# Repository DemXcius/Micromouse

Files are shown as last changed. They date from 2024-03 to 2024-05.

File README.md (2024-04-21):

# Micromouse
# The repository for a third-year engineering design project
This repository contains the design and production files for the Power and Sensor modules of a micro-mouse, as part of the EEE3088F course at UCT 2024 Main Project.

# Project Overview: Micro-Mouse Hardware Design

## What is a Micro-Mouse?
In essence, a micro-mouse is a maze-solving robot. If you're unfamiliar with the concept, watch [Veritasium's](https://www.youtube.com/watch?v=ZMQbHMgK2rw) video to gain a clearer understanding. It's worth noting that while the robots featured in the video may be quite speedy, this micro-mouse will likely (almost certainly) operate at a slower pace. Nonetheless, let the video serve as inspiration.

## Project Description
This project focuses primarily on the design of the micro-mouse's hardware, with some minor software components. The main challenge lies in meeting the project's requirements while adhering to a STRICT budget. To facilitate this endeavor, the project has been divided into four modules: the processor, motherboard, sensing, and power.
The processor and motherboard modules have already been designed and this repository focuses only on the sensing and power modules. 

## Project Modules

### Processor Module: 
This module entails the design of the microcontroller unit responsible for controlling the micro-mouse's actions within the maze. The processor used is an STM32L476.

### Motherboard Module: 
The motherboard serves as the central hub for connecting various hardware components of the micro-mouse. Here, there is leeway as to how the motherboard is designed.

### Sensing Module: 
The project will involve designing and manufacturing the sensing module, which comprises sensors responsible for detecting walls, corners, and other obstacles within the maze.

### Power Module: 
Lastly, the project involves designing and manufacturing the power module, which will provide the necessary electrical power to all components of the micro-mouse.

## Budget Constraint
It's crucial to note that this project had a strict budget constraint imposed. While innovation and creativity are encouraged, all design decisions were made with the budget in mind.

## Project Details:
- Project Focus: Power and sensing module design and manufacturing.
- Connectors: JST PH 2mm pin pitch connector for the battery and a 2x8 (2.54mm pin pitch) pin header for interfacing with the motherboard.
- Budget: $8.25 per board.

## Subsystem Description: Power
- Motor Operation: Controls 2 motors, each capable of drawing up to 200mA, powered by a 1S1P battery.
- Battery Voltage Sensing: Provides an analog connection to sense battery voltage for battery state of charge (SoC) monitoring.
- Battery Charging: Charges the battery from the 5V input pin. Must handle the scenario when 5V is removed.
- ON/OFF Switch: Incorporates an ON/OFF switch with specific power consumption requirements in the OFF and ON states.
  
## Subsystem Description: Sensing
- Sensor Operation: Detects whether there is an obstacle in front of the robot or on its sides.
- Power Saving: Has switching means to save power when not in operation.
- Main Components: 4x TSAL4400 IR LED's, 3x SFH205F photodiodes, 1x LiPo 800mAh 3.7V

- ## Included Files:
- Datasheets: Datasheets for components used in the Power and Sensing modules.
- Production Files: Files required for manufacturing the Power and Sensing module, including Gerber files and Bill of Materials (BOM).
- Schematics: Schematics for Power and Sensing modules.
  
## Usage:
- Clone the repository to access all project files.
- Review the datasheets for component specifications.
- Use the production files for manufacturing the Power or Sensing module PCB's.
- Review and modify the PCB files as needed for customization.
  
- NOTE: Production and files associated with the production were designed and used with [jlcpcb](https://jlcpcb.com/) as the manufacturer in mind.

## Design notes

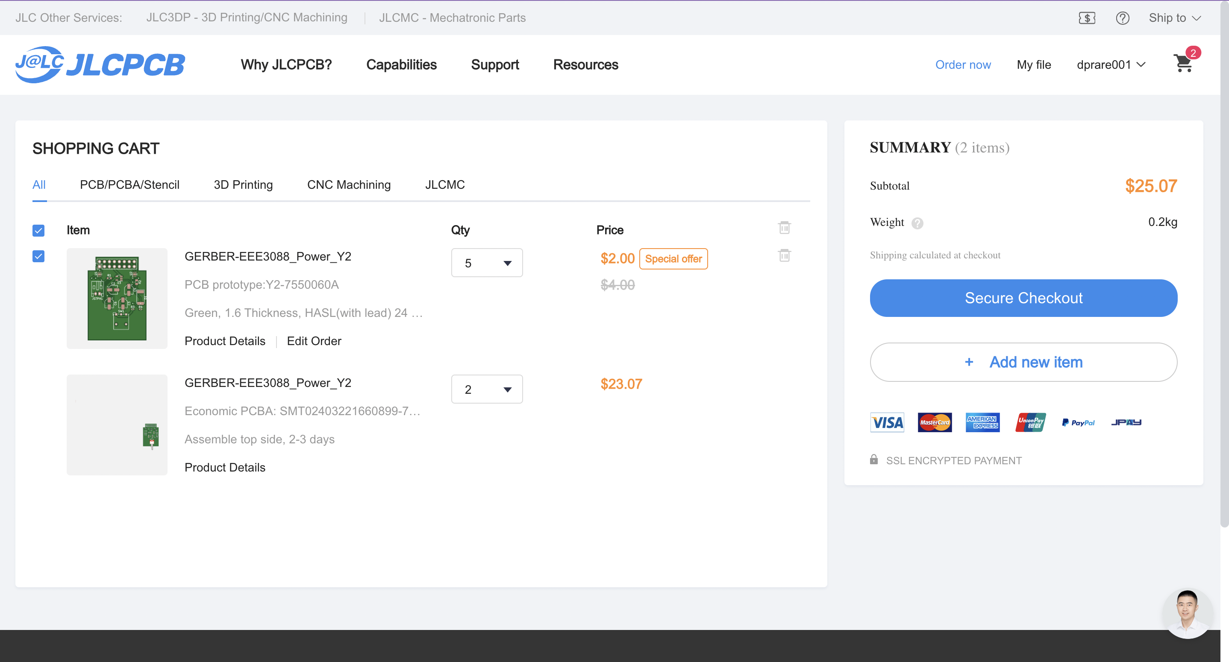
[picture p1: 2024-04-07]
Power Subsystem/EEE3088F_Project_JLCPCBacceptance_DPRARE001.png

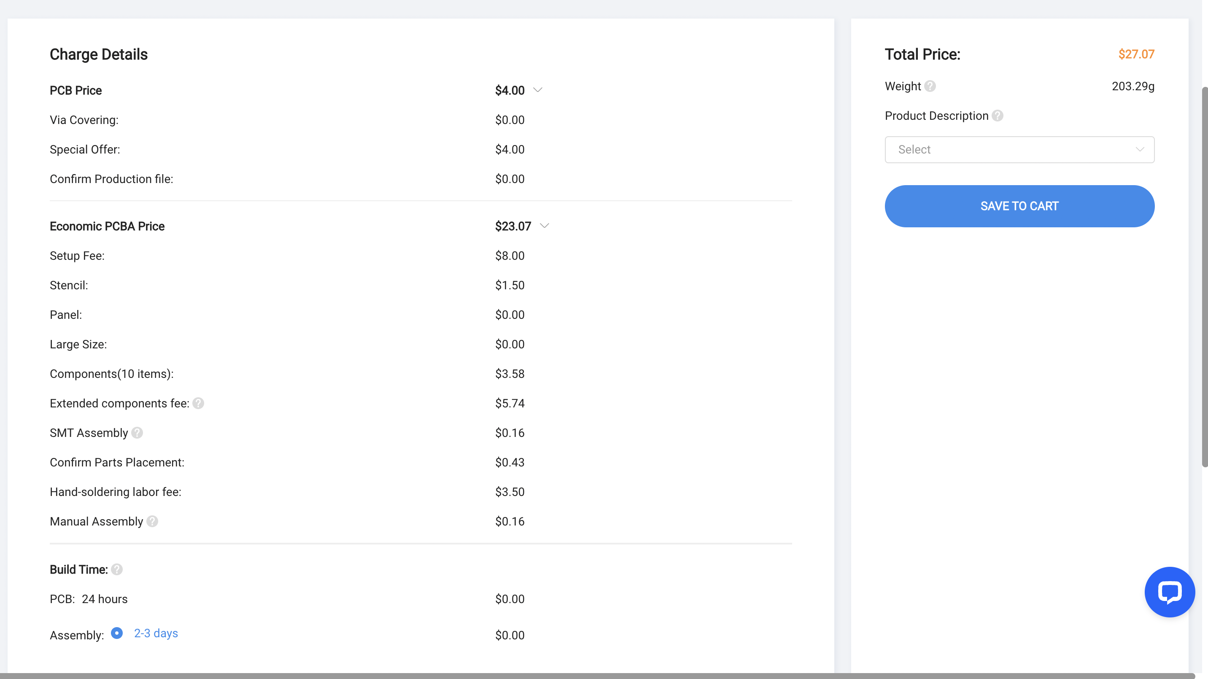
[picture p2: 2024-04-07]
Power Subsystem/EEE3088F_Project_JLCPCBacceptance_DPRARE001 copy.png

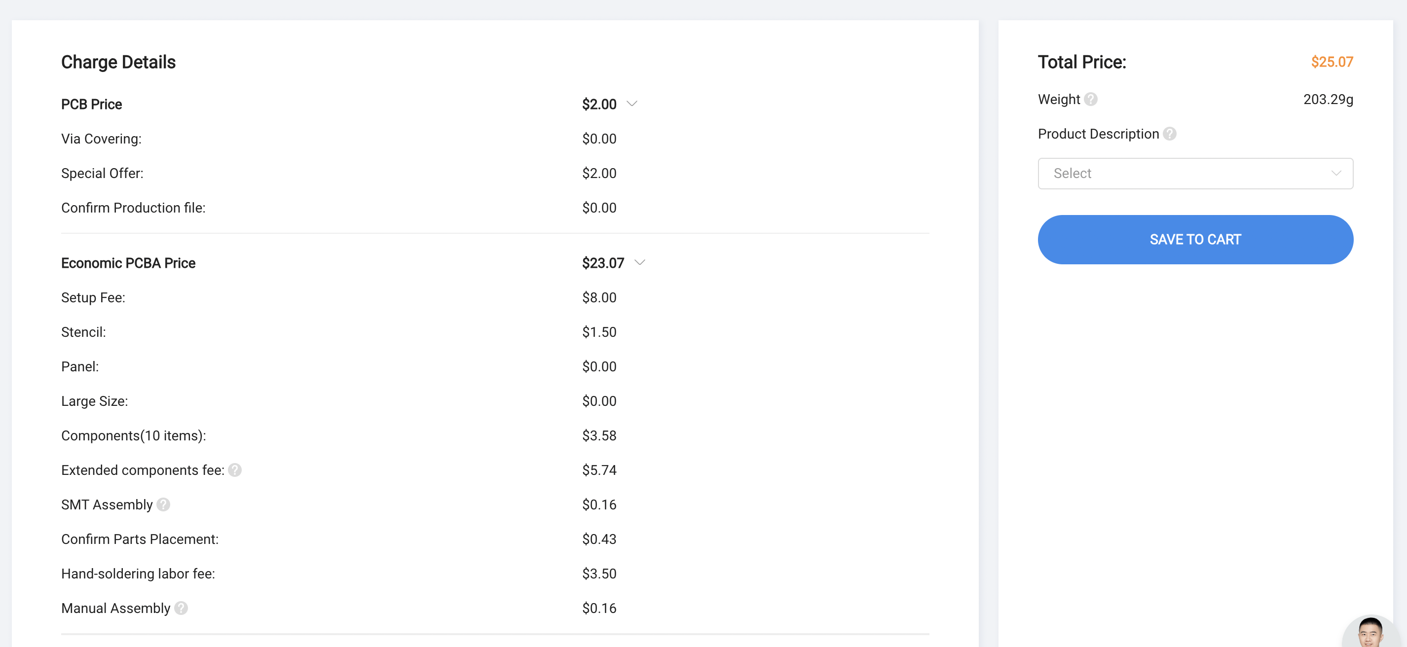
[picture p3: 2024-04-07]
Power Subsystem/EEE3088F_Project_JLCPCBBOM_DPRARE001.png

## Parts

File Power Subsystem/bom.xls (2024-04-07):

Comment | Designator | Footprint | JLCPCB Part #
0.1u | C2,C3 | CP_Elec_4x5.4 | C14663
DRV8837 | U1,U2 | WSON-8-1EP_2x2mm_P0.5mm_EP0.9x1.6mm | C39159
1.2k | R3 | R_0402_1005Metric | C17379
LED | D1 | LED_2512_6332Metric_Pad1.52x3.35mm_HandSolder | C2286
470 | R2 | R_0805_2012Metric | C17710
SW_SPDT | SW1 | SW_Lever_1P2T_NKK_GW12LxH | C1788490
MCP73831-2-OT | U3 | SOT-23-5 | C424093
4.7u | C5,C6 | CP_Elec_4x5.4 | C1779
3k | R4 | R_0402_1005Metric | C4211
2K | R1 | R_0603_1608Metric | C4109

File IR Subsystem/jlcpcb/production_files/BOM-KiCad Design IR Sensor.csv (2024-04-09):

Comment | Designator | Footprint | LCSC
10k | R14,R2,R8 | R_0805_2012Metric | C17414
4.7uF | C2,C4,C6 | C_0805_2012Metric | C1779
300 | R18,R4 | R_1206_3216Metric | C17887
100k | R1,R13,R7 | R_1206_3216Metric | C17900
100 | R17,R3 | R_1206_3216Metric_Pad1.30x1.75mm_HandSolder | C17901
2N2219 | Q1,Q2 | SOT-23 | C2146
100nF | C1,C3,C5 | C_1206_3216Metric | C24497
SFH205F | D1,D2,D7 | LED_SideEmitter_Rectangular_W4.5mm_H1.6mm | C2693588
22 | R10,R11,R12,R15,R16,R9 | R_0402_1005Metric | C2759745
600 | R19,R5 | R_0805_2012Metric | C28636
1000 | R20,R6 | R_1206_3216Metric | C4410
TSAL4400 | D3,D4,D5,D6,D8,D9 | LED_D5.0mm_Horizontal_O1.27mm_Z3.0mm_IRBlack | C94135
SolderJumper_2_Open | JP3 | SolderJumper-2_P1.3mm_Open_RoundedPad1.0x1.5mm
SolderJumper_2_Open | JP2 | SolderJumper-2_P1.3mm_Open_RoundedPad1.0x1.5mm
SolderJumper_2_Open | JP9 | SolderJumper-2_P1.3mm_Open_RoundedPad1.0x1.5mm
SolderJumper_2_Open | JP13 | SolderJumper-2_P1.3mm_Open_RoundedPad1.0x1.5mm
SolderJumper_2_Open | JP11 | SolderJumper-2_P1.3mm_Open_RoundedPad1.0x1.5mm
SolderJumper_2_Open | JP7 | SolderJumper-2_P1.3mm_Open_RoundedPad1.0x1.5mm
SolderJumper_2_Open | JP14 | SolderJumper-2_P1.3mm_Open_RoundedPad1.0x1.5mm
SolderJumper_2_Open | JP12 | SolderJumper-2_P1.3mm_Open_RoundedPad1.0x1.5mm
SolderJumper_2_Open | JP10 | SolderJumper-2_P1.3mm_Open_RoundedPad1.0x1.5mm
SolderJumper_2_Open | JP8 | SolderJumper-2_P1.3mm_Open_RoundedPad1.0x1.5mm
SolderJumper_2_Open | JP6 | SolderJumper-2_P1.3mm_Open_RoundedPad1.0x1.5mm
SolderJumper_2_Open | JP5 | SolderJumper-2_P1.3mm_Open_RoundedPad1.0x1.5mm
SolderJumper_2_Open | JP4 | SolderJumper-2_P1.3mm_Open_RoundedPad1.0x1.5mm
SolderJumper_2_Open | JP1 | SolderJumper-2_P1.3mm_Open_RoundedPad1.0x1.5mm
Conn_02x14_Odd_Even | J1 | PinHeader_2x14_P2.54mm_Vertical

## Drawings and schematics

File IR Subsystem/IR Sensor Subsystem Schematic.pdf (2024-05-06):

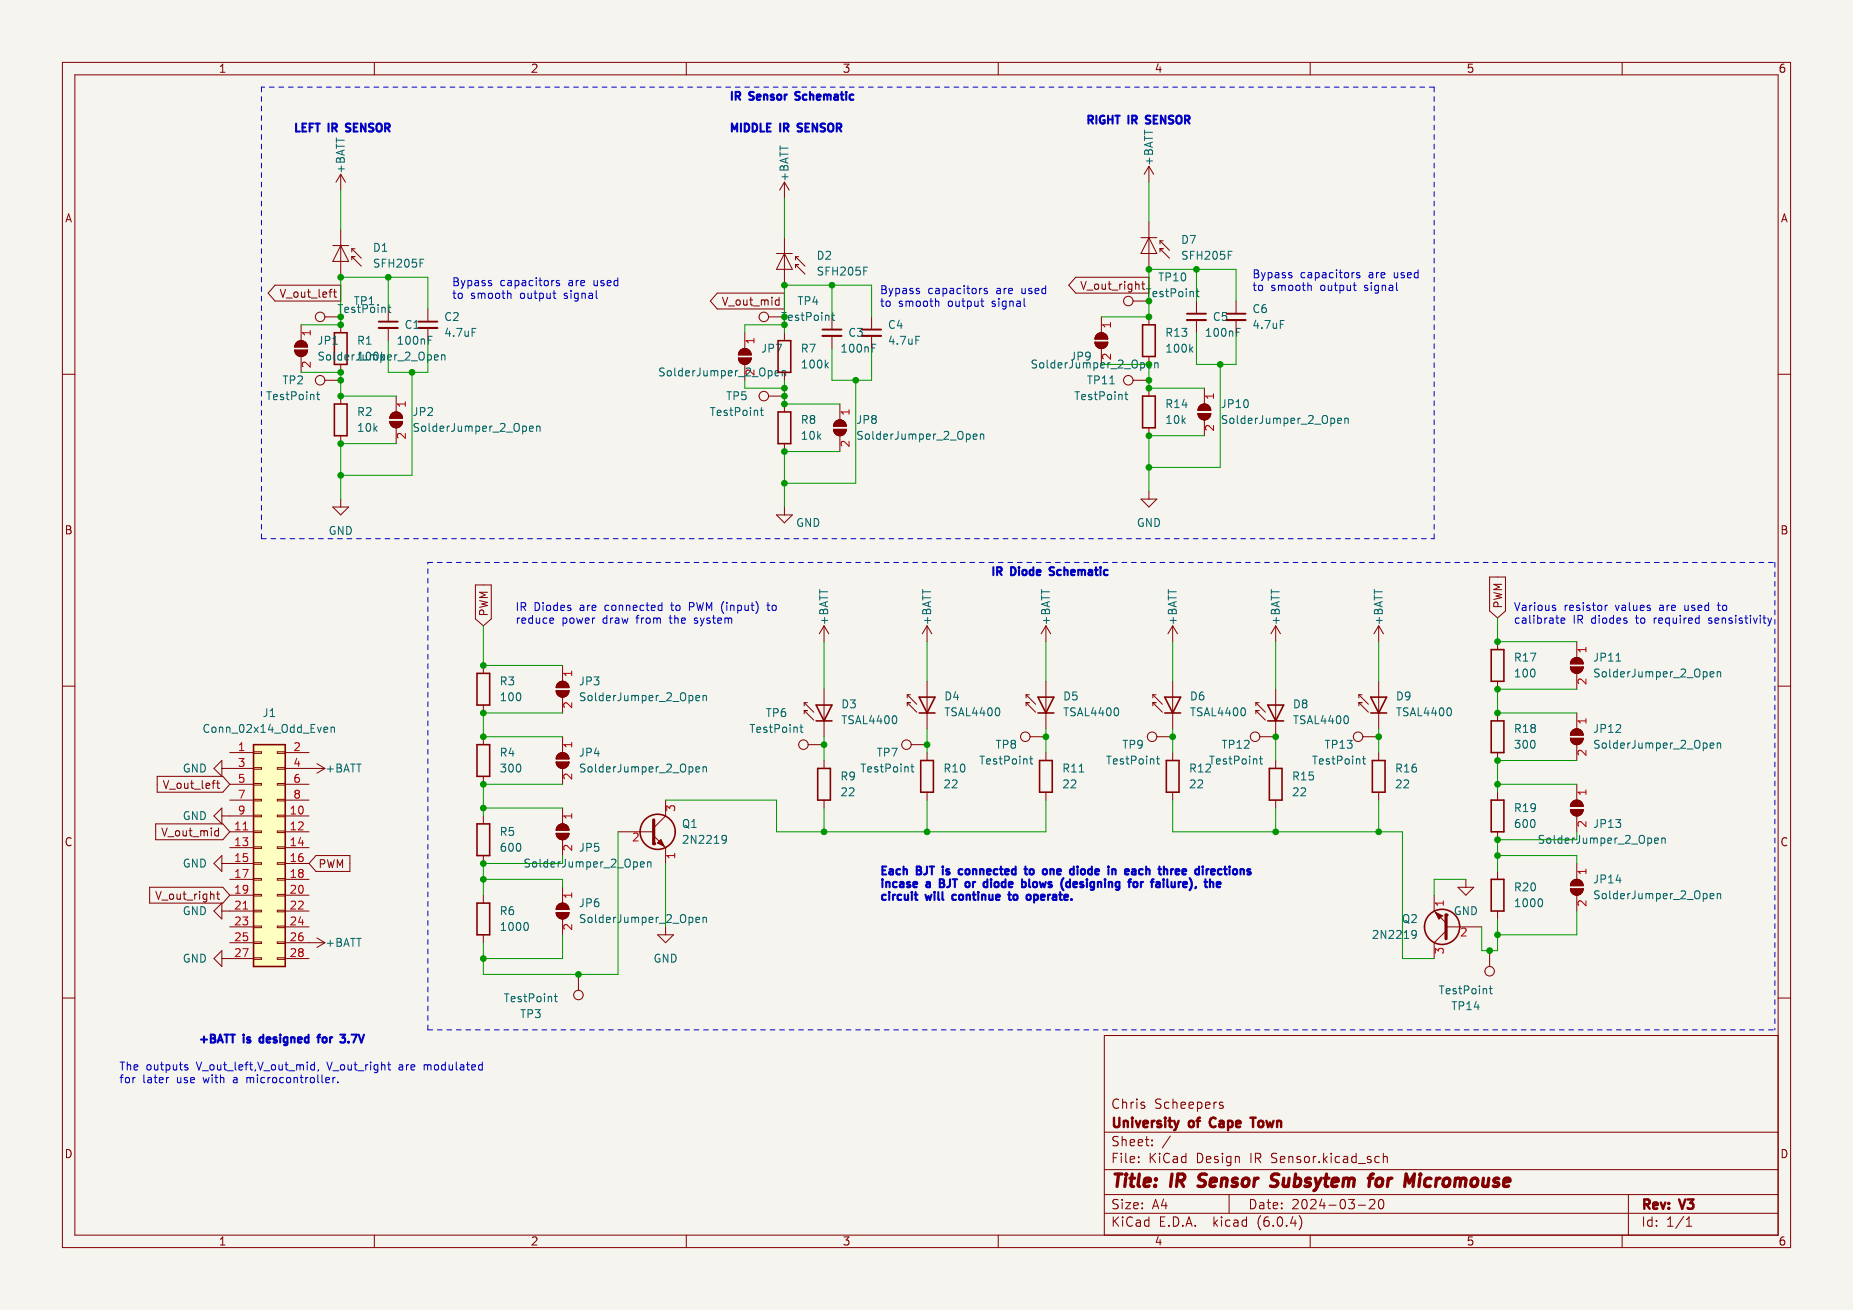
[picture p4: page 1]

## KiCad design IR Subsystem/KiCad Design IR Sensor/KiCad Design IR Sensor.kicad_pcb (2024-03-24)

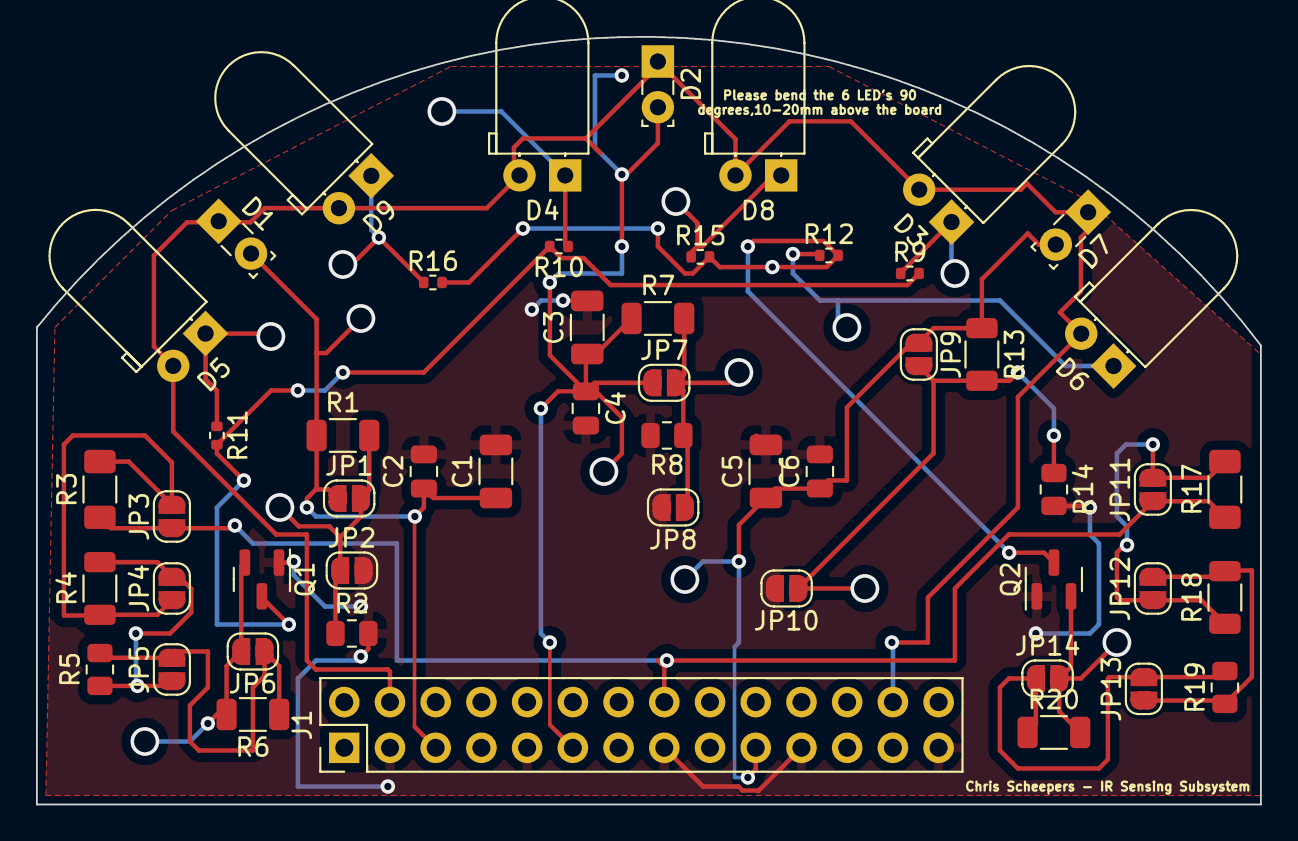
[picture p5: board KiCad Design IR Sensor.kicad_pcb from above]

Board: 2 copper layers, 68.0 x 42.6 mm, 52 parts (0 on the bottom side), 25 nets.

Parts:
C1, C3, C5: 100nF; C_1206_3216Metric
C2, C4, C6: 4.7uF; C_0805_2012Metric
D1, D2, D7: SFH205F; LED_SideEmitter_Rectangular_W4.5mm_H1.6mm
D3, D4, D5, D6, D8, D9: TSAL4400; LED_D5.0mm_Horizontal_O1.27mm_Z3.0mm_IRBlack
J1: Conn_02x14_Odd_Even; PinHeader_2x14_P2.54mm_Vertical
JP1, JP2, JP3, JP4, JP5, JP6, JP7, JP8, JP9, JP10, JP11, JP12, JP13, JP14: SolderJumper_2_Open; SolderJumper-2_P1.3mm_Open_RoundedPad1.0x1.5mm
Q1, Q2: 2N2219; SOT-23
R1, R7, R13: 100k; R_1206_3216Metric
R2, R8, R14: 10k; R_0805_2012Metric
R3, R17: 100; R_1206_3216Metric_Pad1.30x1.75mm_HandSolder
R4, R18: 300; R_1206_3216Metric
R5, R19: 600; R_0805_2012Metric
R6, R20: 1000; R_1206_3216Metric
R9, R10, R11, R12, R15, R16: 22; R_0402_1005Metric

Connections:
+BATT: D1.1 (K), D2.1 (K), D3.2 (A), D4.2 (A), D5.2 (A), D6.2 (A), D7.1 (K), D8.2 (A), D9.2 (A), J1.4, J1.26
GND: C1.2, C2.2, C3.2, C4.2, C5.2, C6.2, J1.3, J1.9, J1.15, J1.21, J1.27, JP2.2 (B), JP8.2 (B), JP10.2 (B), Q1.1 (E), Q2.1 (E), R2.2, R8.2, R14.2
unnamed: D3.1 (K), R9.1
unnamed: D4.1 (K), R10.1
unnamed: D5.1 (K), R11.1
unnamed: D6.1 (K), R12.1
unnamed: D8.1 (K), R15.1
unnamed: D9.1 (K), R16.1
unnamed: JP1.2 (B), JP2.1 (A), R1.2, R2.1
unnamed: JP3.2 (B), JP4.1 (A), R3.2, R4.1
unnamed: JP4.2 (B), JP5.1 (A), R4.2, R5.1
unnamed: JP5.2 (B), JP6.1 (A), R5.2, R6.1
unnamed: JP6.2 (B), Q1.2 (B), R6.2
unnamed: JP7.2 (B), JP8.1 (A), R7.2, R8.1
unnamed: JP9.2 (B), JP10.1 (A), R13.2, R14.1
unnamed: JP11.2 (B), JP12.1 (A), R17.2, R18.1
unnamed: JP12.2 (B), JP13.1 (A), R18.2, R19.1
unnamed: JP13.2 (B), JP14.1 (A), R19.2, R20.1
unnamed: JP14.2 (B), Q2.2 (B), R20.2
unnamed: Q1.3 (C), R9.2, R10.2, R11.2
unnamed: Q2.3 (C), R12.2, R15.2, R16.2
PWM: J1.16, JP3.1 (A), JP11.1 (A), R3.1, R17.1
V_out_left: C1.1, C2.1, D1.2 (A), J1.5, JP1.1 (A), R1.1
V_out_mid: C3.1, C4.1, D2.2 (A), J1.11, JP7.1 (A), R7.1
V_out_right: C5.1, C6.1, D7.2 (A), J1.19, JP9.1 (A), R13.1

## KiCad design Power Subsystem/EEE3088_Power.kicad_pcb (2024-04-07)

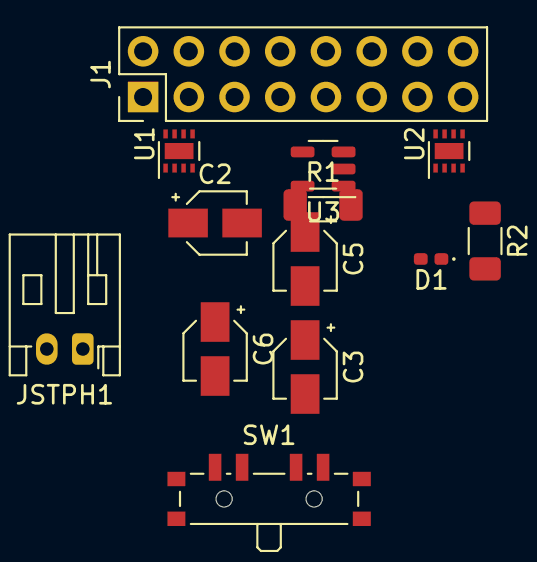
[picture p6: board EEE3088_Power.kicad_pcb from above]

Board: 2 copper layers, 13 parts (0 on the bottom side), 16 nets, no tracks yet.

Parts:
C2, C3: 0.1u; CP_Elec_3x5.3
C5, C6: 4.7u; CP_Elec_3x5.3
D1: LED; D_0402_1005Metric_Pad0.77x0.64mm_HandSolder
J1: Conn_01x16_Male; PinHeader_2x08_P2.54mm_Vertical
JSTPH1: Conn_01x02_Female; JST_PH_S2B-PH-K_1x02_P2.00mm_Horizontal
R1: 2K; R_1206_3216Metric_Pad1.30x1.75mm_HandSolder
R2: 470; R_1206_3216Metric_Pad1.30x1.75mm_HandSolder
SW1: SW_SPDT; SW_SP3T_PCM13
U1, U2: DRV8837; WSON-8-1EP_2x2mm_P0.5mm_EP0.9x1.6mm
U3: MCP73831-2-OT; SOT-23-5

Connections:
/+5V: C5.1, D1.2 (A), J1.11, U3.4 (VDD)
/BATT1: J1.7, JSTPH1.1, SW1.2 (B)
/BATT2: J1.8, JSTPH1.2
/BATT+: C2.1, C3.1, C6.1, SW1.1 (A), U1.1 (VM), U1.7 (~SLEEP), U1.8 (VCC), U2.1 (VM), U2.7 (~SLEEP), U2.8 (VCC), U3.3 (VBAT)
/Motor1_A: J1.13, U2.2 (OUT1)
/Motor1_B: J1.15, U2.3 (OUT2)
/Motor2_A: J1.1, U1.2 (OUT1)
/Motor2_B: J1.3, U1.3 (OUT2)
/PC6: J1.2, U1.6 (IN1)
/PC7: J1.4, U1.5 (IN2)
/PC8: J1.14, U2.6 (IN1)
/PC9: J1.16, U2.5 (IN2)
GND: C2.2, C3.2, C5.2, C6.2, J1.5, J1.6, R1.2, SW1.3 (C), U1.4 (GND), U1.9 (GND), U2.4 (GND), U2.9 (GND), U3.2 (VSS)
unnamed: D1.1 (K), R2.2
unnamed: R1.1, U3.5 (PROG)
unnamed: R2.1, U3.1 (STAT)

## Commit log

2024-03-24 PCB Design complete.
    Final upload to repo before submission of Gerber files.
2024-03-24 Deleted IR Sensor directory
    Uploading a new sub-directory after this.
    [BOM-KiCad Design IR Sensor.csv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]
2024-03-24 Final Submission for PCB Design
    [KiCad Design IR Sensor.kicad_pcb, KiCad Design IR Sensor.kicad_sch]
2024-03-24 JLCPCB prod. files
    BOM, CPL and Gerber Files
2024-04-09 Changed IR Sensor Section Format
    [KiCad Design IR Sensor.kicad_pcb, KiCad Design IR Sensor.kicad_sch]
2024-04-09 Removed KiCad Design IR Sensor-backups
2024-04-09 Uploaded IR Subsytem Schematic
2024-04-17 Create Gerbers
